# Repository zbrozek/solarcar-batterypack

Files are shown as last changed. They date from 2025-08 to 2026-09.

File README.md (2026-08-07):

# Open-source battery pack for solar cars
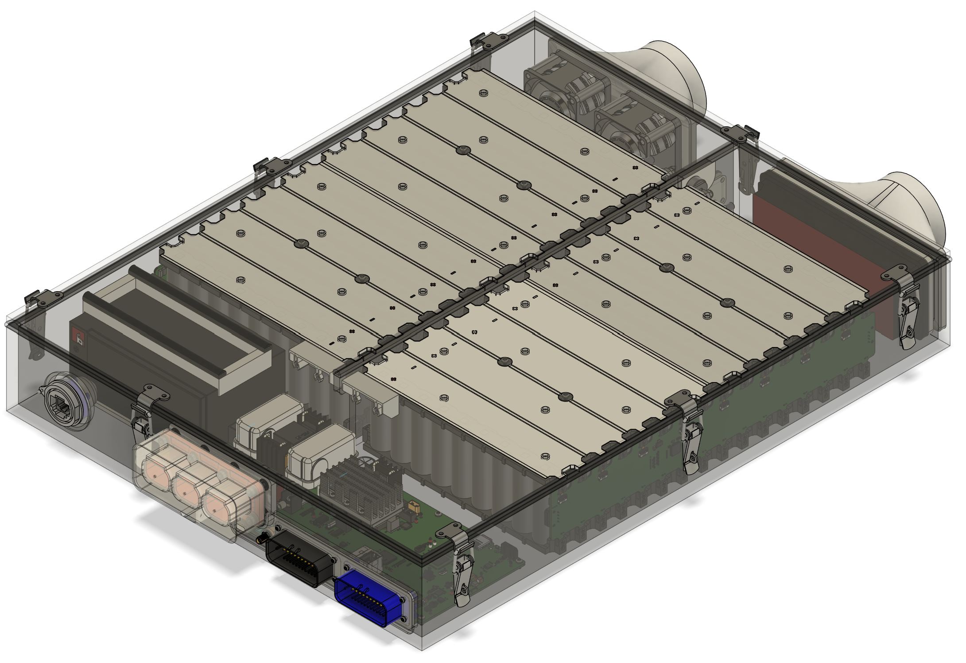
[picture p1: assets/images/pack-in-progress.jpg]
Image of battery pack


## What is this?
This is the mechanical and electronic design for a battery pack intended for solar cars competing in common races like ASC or WSC. It's designed to be reasonably easy to fabricate and assemble, but without significantly compromising the quality of the design.

## Who are you?
I'm Sasha Zbrozek and I was trained as an electrical engineer. I was on Stanford's solar car team from 2006 through 2010 and continue to participate with them and the broader solar car community from the comfort of my golden years. I have a normal day job that takes up most of my time, but we've all got to have hobbies.

## Why did you make this?
I participated as a staff member in the 2025 Formula Sun Grand Prix and enjoyed working with the students immensely. I think the community would benefit from having more open-source content available for students to take, modify, and improve.

And why a battery pack specifically? I felt that many cars under-engineered them and that there was a lot of room to try and introduce improvements that would have both performance and safety benefits for solar racing as a whole.

## Are you going to open-source the BMS too?
I did! Check the "bms" folder. This is an expansive design with way more features that most teams are going to use. There's a lot of electronic content in there that teams might want to use even if they aren't using this design in its totality. Check out:
- The MP6519 current regulator sheet for contactor coil economization.
- The HV architecture page and its very-aggressive precharge.
- The HV bleed page for an extremely simple DC bus safety enhancement implementation.

## Key design decisions and their motivations
### 32s9p arrangement
This pack is a 32 series, 9 parallel (32s9p) arrangement of [21700 cells](https://www.molicel.com/wp-content/uploads/Product-Data-Sheet-of-INR-21700-P50B-80122.pdf). This gives 134.4 volts top-of-charge with typical NMC cells. Using a power-of-two number of cells in series makes for really convenient bussing, allowing all bolted terminals to be on the top of the modules and for a wide range of module shapes. The voltage is reasonably safe for the Wavesculptor 22 and matches well with the super-beefy [MDE 30KPA132A TVS diode](https://mm.digikey.com/Volume0/opasdata/d220001/medias/docus/4180/30KPA_Series.pdf).

### Hybrid bus bars
Simple nickel sheet is pretty resistive and also dense. This design uses [aluminum bus bars with nickel inserts](https://www.everbestbattery.com/index.php?m=home&c=View&a=index&aid=171) for easy welding and high conductivity. Folded sheet metal also affords the opportunity for built-in studs for easy bolting where bolted joints cannot be avoided.

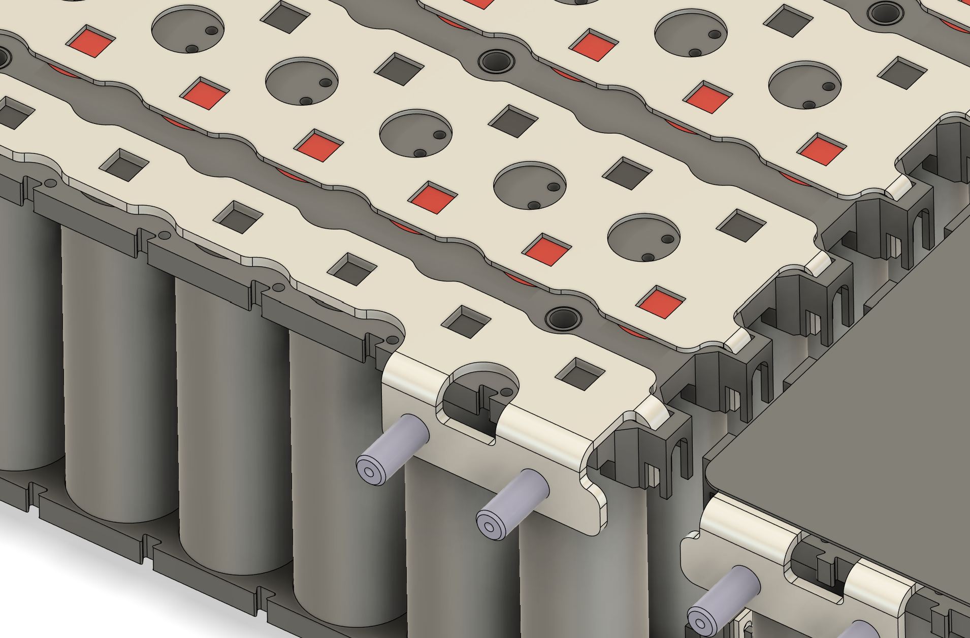
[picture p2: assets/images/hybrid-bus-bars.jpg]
Image of bus bars


### Large modules
This design uses only two 16s9p modules in order to dramatically cut down on the number of high-current bolted joints. Those are failure-prone and can easily cause battery pack fires by igniting nearby plastics if the bolted joints lose preload and become high impedance.

This is likely to be a controversial choice; teams often want their packs to be more modular in order to have a smaller minimum serviceable unit. In my experience, packs get built once and then basically never touched again outside of reworks to address manufacturing defects. My goal is to enable a high-quality module to be built, tested, and installed once.

### Cell monitoring on the side of the module
There is a large PCBA that mounts to the side of the module and is supposed to hold all of the cell monitoring and balancing electronics. This is to try and reduce the amount of wire harnessing inside of the battery pack, which is often failure-prone and easily shorted by accident.

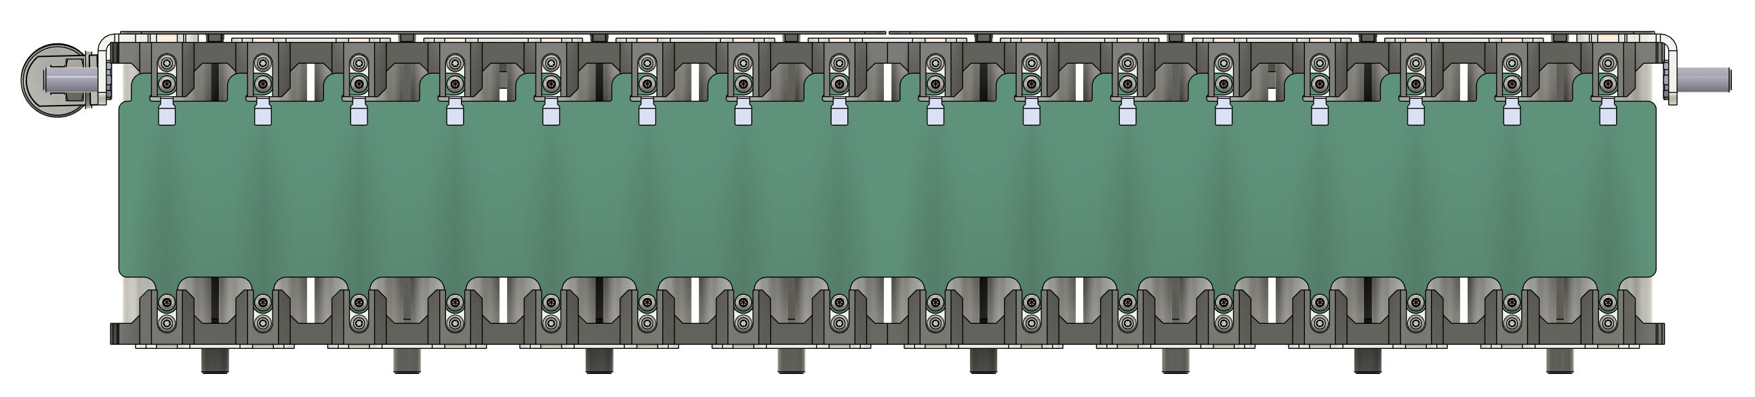
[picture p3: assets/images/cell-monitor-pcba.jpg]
Image of cell monitoring PCBA


### Mostly sealed
Aside from the deliberate air ingest and exhaust paths, the battery pack is theoretically sealed (assuming good manufacturing quality). Solar cars don't always enjoy sunny weather, so it's important to keep dust and water out. It uses the engine air filter to keep out dust.

### 3D-printed cell spacer plates
The cell spacer plates are intended to be 3D printed in [PC FR](https://us.store.bambulab.com/products/pc-fr) with a 0.2 mm nozzle. I used a Bambu H2D. There are a number of features that would be difficult or impossible to replicate without 3D printing, like the zero-draft shields that prevent you from losing screws into the forest of cells:

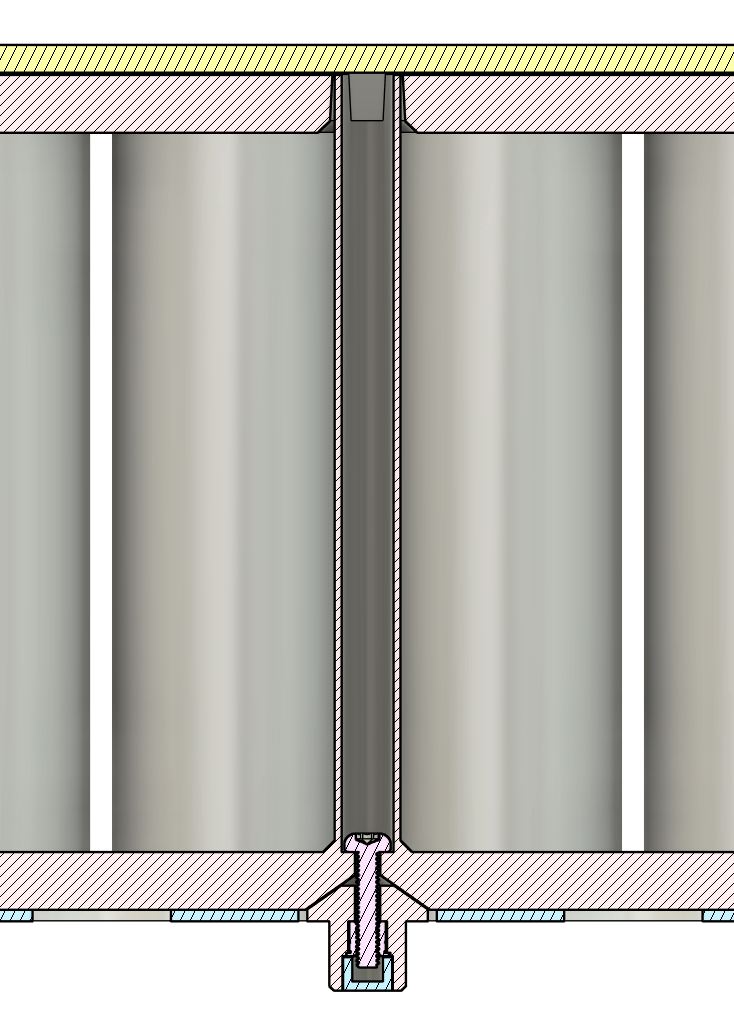
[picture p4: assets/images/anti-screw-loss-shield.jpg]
Image of an anti-screw-loss shield.


...or the fluid channels that deliver low-viscosity glue to hold the cells in place:

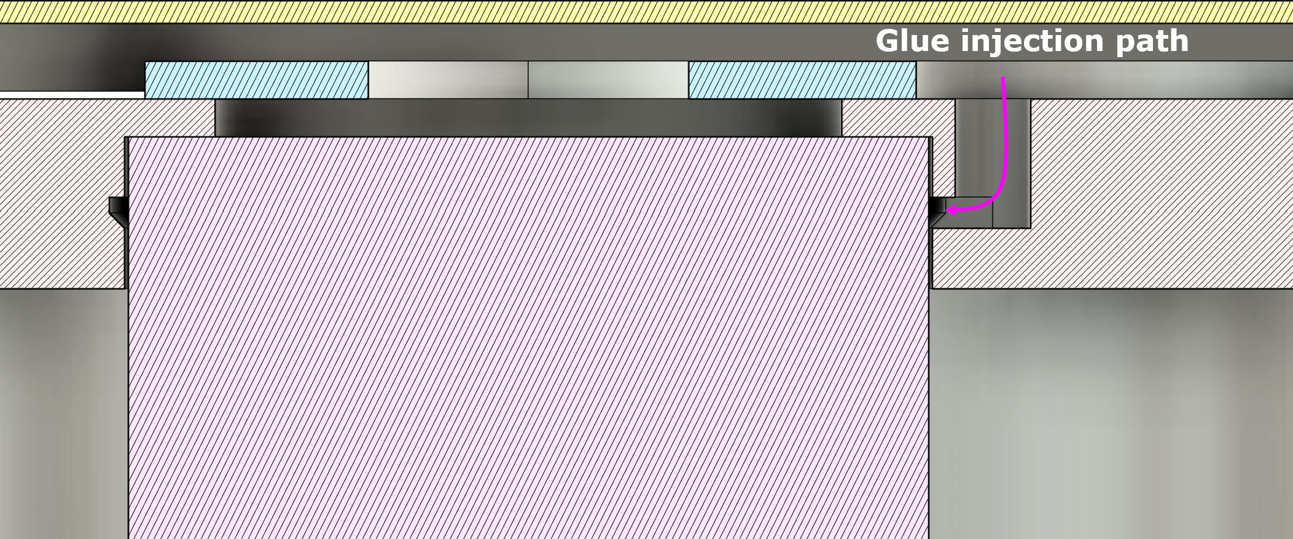
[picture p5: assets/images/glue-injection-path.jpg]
Image of a fluid channel for glue delivery for cell retention.


**Do not print parts without calibrated shrinkage calibration.** This design is not tolerant of undersized plastic parts.

### Mid-pack main fuse
A mid-pack fuse is a convenient way to halve the available electric potential (and thus quarter the available fault power) after a fault or during service. I prefer them to high- or low-side fuses. The mid-pack installation location also leverages the pack symmetry to reduce the total number of bolted joints.

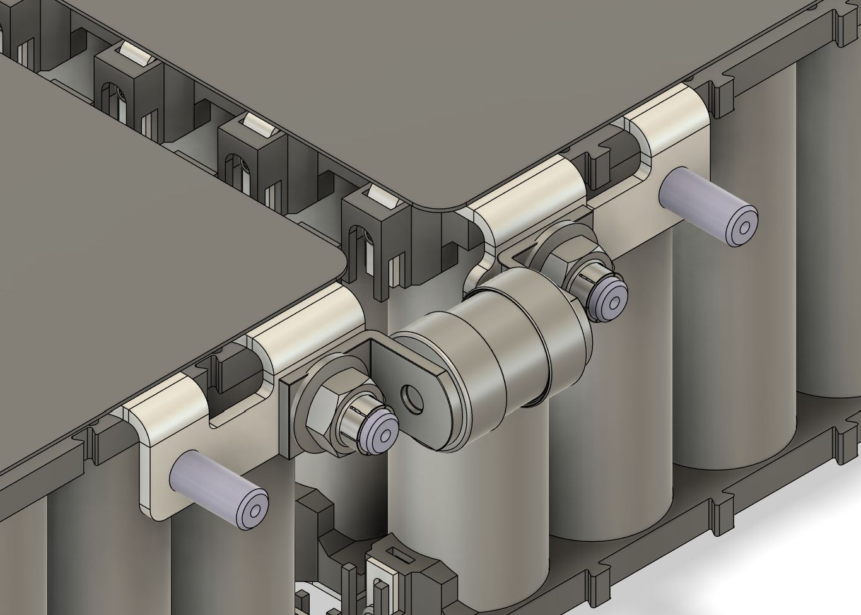
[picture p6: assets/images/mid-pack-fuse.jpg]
Image of a fuse installed at the pack midpoint.


### Shields
There are baffles that make it difficult to accidentally contact the sense taps on the bent parts of the bus bars:

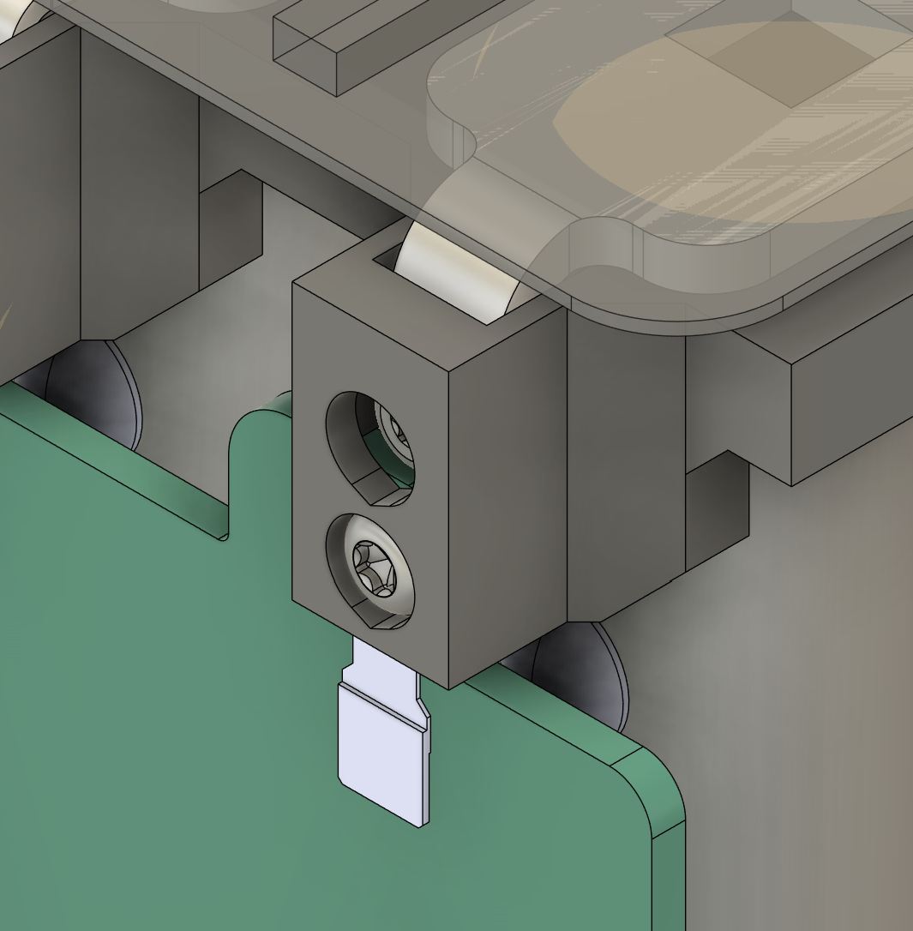
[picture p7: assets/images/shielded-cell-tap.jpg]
Image of a voltage sense tap with shielding plastic which makes it hard to accidentally contact the terminal.


There are also shields which go on the top side of the modules to reduce risks associated with leans and drops:

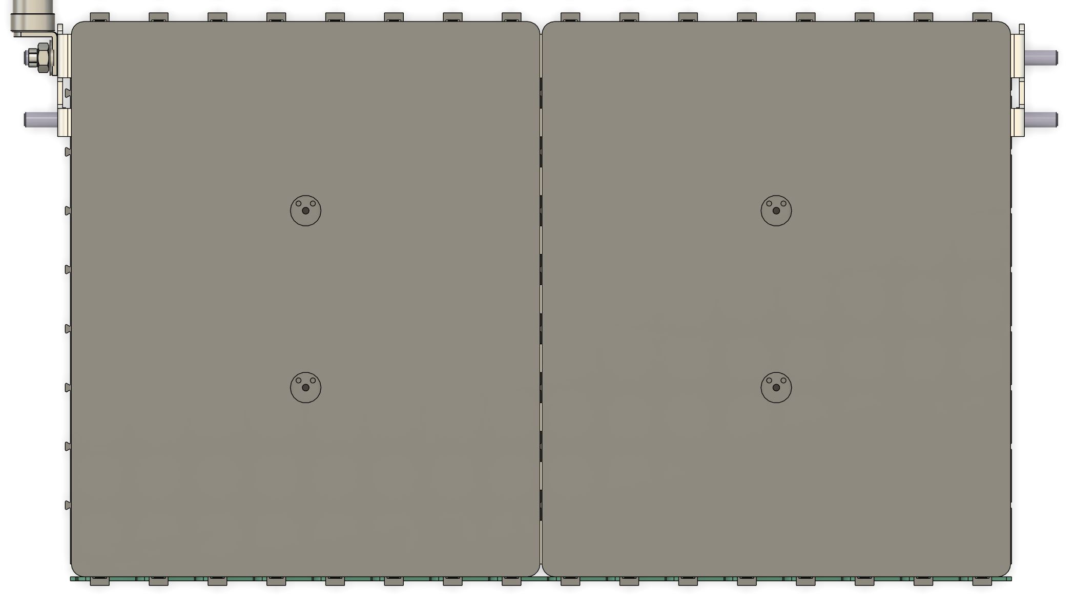
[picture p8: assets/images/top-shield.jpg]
Image of a plastic shields covering bus bars.


### Assembly aids
This design will come with a number of assembly aids to help with ergonomics, safety, or assembly quality. The first of these is a temporary handle that gets attached via screws from above while lifting and lowering the large modules into place into the battery pack.

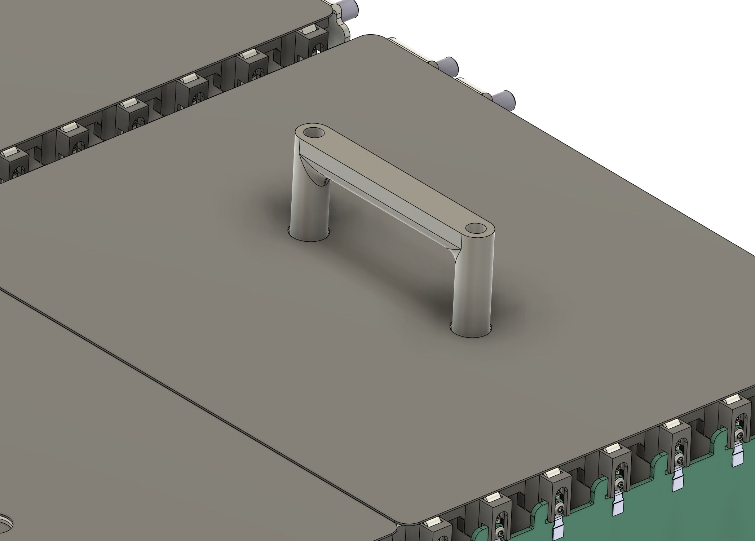
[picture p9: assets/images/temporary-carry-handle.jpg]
Image of a carry handle.


## What's not done yet?
Lots! Off the top of my head:
- There is no plug (airflow baffle) for the harness passthrough between the two cell monitoring boards.
- There is no fuse cover yet.
- I don't like the LV battery retention scheme and will probably do it again.
- Need to design assembly aids for centering the aluminum plates when gluing them to the chassis.
- Need to design assembly aids for setting the hasp Z height correctly.

## How do I use this?
A team looking to use this design will probably want to fork it and modify it to suit their vehicle. If you have any ideas for improvements, please file issues or create PRs and I'll consider including them upstream. Note that WSC and ASC have differing pack energy limitations, and so you may need to alter the number of parallel cells to match.

As this design matures I'll create additional documentation for things like the shopping list, tools needed for fabrication, and an assembly guide. For now, you'll need at least these tools and capabilities to reproduce the design:

- Ability to buy things from China with a wire transfer (bus bars)
- Ability to buy things from typical online vendors with a credit card (everything else)
- Ability to fixture an assembly and use epoxy to put it together
- Cell spot welding
- 3D printing in appropriate materials, primarily PC FR.
- Routing / milling of large sandwich panels
- Standard and long reach Torx drivers

## What are current versions?
I really need to use the GitHub release feature to make cohesive bundles of buildable artifacts. Until then, if you're building _right now_:
- The mechanical design is up-to-date. If there's a file missing, please file an issue.
- bms_afe-1_1
- Don't build any bms_afe_tester for now. That design is getting overhauled.
- bms_mainboard-1_0 (1.1 is coming end of August 2026)
- bms_fan_breakout-1_0

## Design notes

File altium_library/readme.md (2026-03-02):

# Theory of operation

These libraries are stored in CSV files, one table per file. Each table has fields that point to specific SchLib and PcbLib files and entries for symbols and footprints. The Windows ODBC system provides a local connection to the files.

Altium uses the dblib file to know what database to use. It also specifies field mappings for each table (CSV file). A user needs to use the "ODBC data sources (64-bit)" tool to get Windows to expose the CSV files as a SQL database.

# Getting started

Under the "User DSN" tab, hit "add", then select "Microsoft Access text driver". Give it the name "solarcar-altium-db", uncheck "use current directory", and select the "tables" directory in this repository. "OK" all the way out of the tool, restart Altium, and ensure that the dblib can connect to the ODBC provider and open the tables.

# Scripts

In the 'scripts' folder are some tools for downloading the JLCPCB library from yaqwsx. It'll come as a multi-part zip containing a sqlite database. The other tool parses that out into various CSV tables for use with Altium.

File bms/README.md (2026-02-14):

## bms_mainboard

Overall, this is a complicated and excessive kitchen sink of functionality. Its primary function is managing the battery pack state machine and driving the contactors accordingly. Beyond that, however, it is effectively a full central vehicle computer. There are some choices that seasoned solar car teams might find unusual.

The contactors are provided onboard. Most solar cars use dramatically bigger wires and contactors than they actually need. By right-sizing these devices, they can fit onto a PCBA. Current sensing is done via onboard shunt resistors in order to avoid more interconnects. This simplifies the wiring of the battery pack tremendously, reducing opportunities for errors and failures. There is also an automatic high voltage bus discharge when the system is powered down. All three contactors are driven with current regulators, enabling fine-grained control of coil currents in order to reduce system power consumption.

An onboard Ethernet switch provides Ethernet connectivity from the onboard STM32 microcontroller both to other on-vehicle devices as well as to an uncommitted RJ-45 receptacle intended for easy debugging. Some - maybe most - teams won't utilize this feature, preferring to stick to the more-familiar CAN (also provided). Beyond being simply much faster, Ethernet also offers point-to-point links which make the network (mostly) topology insensitive. There is no worrying about whether or not the bus remains terminated as the system topology changes.

The exception to the above is the speculative inclusion of a 10BASE-T1S PHY on the topshell-facing (blue Ampseal 35-position) connector. This is the IEEE 802.3 committee's answer to CAN. It is a 10 mbps multi-drop physical layer for Ethernet that carries traditional Ethernet frames. I will very-likely design MPPTs that use this bus. 

There are also some affordances for improved data gathering about the vehicle. An onboard IMU (3-axis acceleromter plus 3-axis gyroscope) can be used to capture information about vehicle dynamics or to try and estimate incline. An onboard GNSS receiver can be used to provide system time and capture vehicle location or to calibrate wheel odometry. An onboard MicroSD slot allows teams to log telemetry data locally in order to be independent of wireless telemetry systems.

An isolated DC/DC converter produces the low voltage power for the vehicle. It is permanently connected to a low voltage (nominally "12 volt") battery. That battery floats the low voltage bus, absorbing transient loads, but providing net-zero energy to the system. Hypercompetitive teams will probably be annoyed that the system does not afford a battery for allowed off-the-books loads. This is an opinionated choice on my part; I think reliability is more important and this reduces the amount of system state that needs to be tracked and babysat.

There is a current-loop called "EDISC" that must be completed in order for the BMS to receive power. This is intended to be sent to any number of series-connected on/off switches to turn the car on and off. A potentially-controversial feature is the ability for the main microcontroller tor read that loop and force-keepalive the system. This is intended to enable software-driven soft-shutdown procedures.

Finally, there are some protected high-side switches that can be used to drive lights or horns or other loads, as well as some analog and digital inputs for things like throttle sensors and switches.

## bms_afe

The mainboard does *not* sense battery voltages. The "analog front end" board does. It is mounted directly to the battery module to minimize pack wiring and opportunities for failure. This is admittedly annoying to assemble, but since that is a one-time procedure I consider it to be tolerable.

It is built around a TI BQ79616 cell monitoring chip and follows the provided application schematic closely. The board uses the eight remaining GPIO pins (which can be multiplexed to the on-chip ADC) to read NTC thermistors.

These boards can be connected to the mainboard or daisy-chained via twisted pair cables.

## bms_afe_tester

This is a development and test tool. It mates to the AFE board and has sixteen adjustable-output isolated flyback converters to drive the cell tap inputs. It's powered from USB-C PD at 12 volts and can communicate via a second USB-C port or via Ethernet. Hopefully teams use this for scripted automatic testing of their BMS software.

Another use for this is during scrutineering. I hope that teams will bring spare AFE boards and an AFE tester board so that they can easily demonstrate BMS behavior to scrutineers. Clip points are provided in case a team wants to override a flyback's output with an external supply. If doing that, set that channel's output to its lowest-possible voltage and then externally drive to a higher voltage.

## bms_fan_breakout

This is a simple board to break out from an 8-pin FPC cable to two PC-compatible 4-pin fan headers.

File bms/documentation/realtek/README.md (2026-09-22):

The RTL8152B does not have vendor-available documentation, yet it is easily purchaseable through LCSC. I've copied references and tools found on the internet into this repo for ease of use.

[RTL8152B-VB-CG datasheet](https://ftp.infania.net/pub/Windows%20Drivers/Realtek/NIC/RTL8152B-VB-CG_Datasheet_1.2.zip)
[RTL8152B-VB-CG reference schematic](https://ftp.infania.net/pub/Windows%20Drivers/Realtek/NIC/RTL8152B_REFERENCE_SCHEMATIC_V103.zip)
[Windows PG Tool](https://download3.terra-master.com/Utilities/A%20USBLAN%202.5G/A-USBLAN-2.5G_WIN_USB_PGTOOL_v2.0.13_V3.zip)
[Linux PG Tool](https://chromium.googlesource.com/chromiumos/third_party/hdctools/+/master/servo/scripts/servo_mfg/rtunicpg-x86_64)

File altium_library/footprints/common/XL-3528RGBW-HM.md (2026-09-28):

# XINGLIGHT XL-3528RGBW-HM 3D model

`XL-3528RGBW-HM.step` is a colored STEP AP214 file in millimeters. Five solids
represent the molded body and four contacts. The flat black bezel and opaque
white diffuser are colored faces of the body, so they add no thickness or
extra solids. This is the unlit appearance. Hidden dies, bond wires and
internal leadframe geometry are omitted.

## Altium placement

The model matches the origin and pin orientation of `LED_RGB_SMD3528-4P` in
`led_rgb_smd3528-4p.PcbLib`. Use X=0, Y=0, Z=0, rotations=0, scale=1.
The contact undersides are at **Z=0**, with the top at **Z=1.90 mm**.
Looking down from +Z with +Y upward, the marked pin-1 corner is lower right.

| Pin | Function | Existing pad center X | Existing pad center Y |
| --- | --- | ---: | ---: |
| 1 | Red cathode | +1.35 | -0.75 |
| 2 | Common anode | -1.35 | -0.75 |
| 3 | Green cathode | +1.35 | +0.75 |
| 4 | Blue cathode | -1.35 | +0.75 |

Pads are 0.90 x 0.90 mm. The four contacts fit entirely inside their matching
pad outlines. Their envelope centers are X=+/-1.39 mm and Y=+/-0.75 mm.

## Dimensions and sources

The repository's [XINGLIGHT datasheet](../../../../bms/documentation/xinglight/XL-3528RGBW-HM.pdf),
page 9, supplies the dimensions and pinout. Page 1 supplies the exterior
reference illustration. Public manufacturer references are the
[product page](https://www.xinglight.cn/index.php?c=show&id=3412) and its
[datasheet](https://www.xinglight.cn/uploadfile/202511/505682b0e27017b.pdf).

| Feature | Model dimension (mm) |
| --- | ---: |
| Overall X, including contacts | 3.50 |
| Body maximum X | 3.20 |
| Body Y | 2.80 |
| Overall height | 1.90 |
| Contact width along Y | 0.70 |
| Contact pitch along Y | 1.50 |
| Contact rise above seating plane | 1.10 |
| Underside contact envelope length along X | 0.72 |

The drawing also labels the underside contact gap as 2.0 mm. That differs
from 3.50 - 2 x 0.72 = 2.06 mm. The model preserves the stated overall width
and contact length, giving a 2.06 mm gap. The 0.06 mm difference is within
the drawing's general +/-0.25 mm tolerance. Nominal dimensions are modeled;
this is not a maximum-tolerance clearance envelope.

The following undimensioned details are approximate: 2.40 mm diffuser
diameter, 0.20 mm contact-foot thickness and housing standoff, 0.05 mm side
draft in X, 0.04 mm contact bend radius, and the roughly 0.6 mm polarity
corner ending 0.3 mm below the top. The circular diffuser is flush and opaque,
consistent with the mist-white material and reference illustration. Colors
are approximate. Fine underside molding relief is simplified.

The old footprint extrusion is a 3.2 x 3.2 mm square. This model follows the
datasheet's 3.2 x 2.8 mm molded body. The PcbLib has not been modified.

## Validation and regeneration

The exported file was re-imported into FreeCAD/Open CASCADE and checked for
five valid solids, preserved face colors, contact surfaces at Z=0, contact
alignment within the existing pads, and the 3.50 x 2.80 x 1.90 mm overall
envelope. No solids overlap in volume. Isometric, top and bottom renders of
the re-imported STEP were inspected. Import into Altium itself was not tested.

The generator is `../../scripts/build_xl3528_step.py`. From the repository root:

```powershell
& 'C:\Program Files\FreeCAD 1.0\bin\python.exe' altium_library\scripts\build_xl3528_step.py --render --qa-dir tmp\xl3528
```

FreeCAD 1.0 was used. VTK is required only for the optional preview render.
The generator needs no network access or additional asset files.

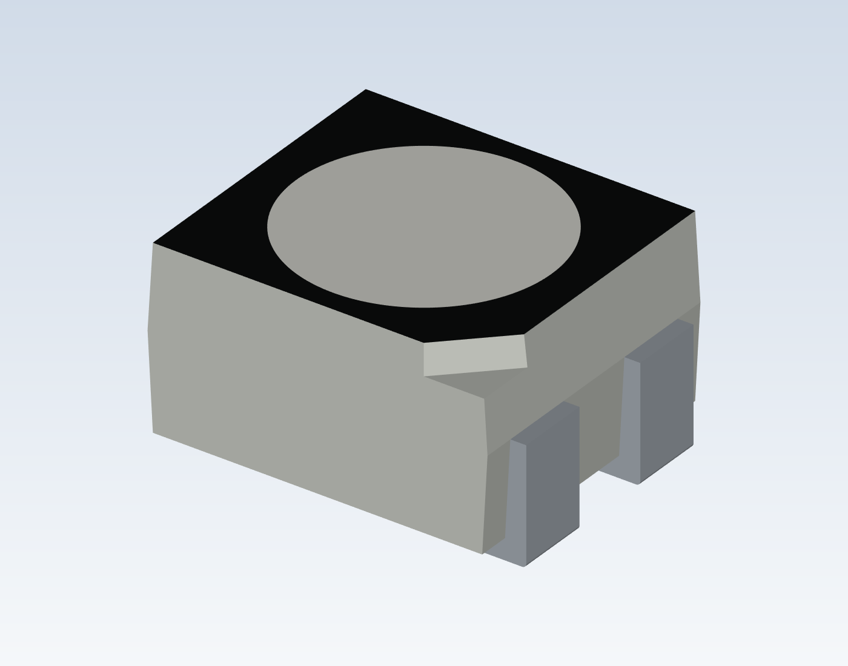
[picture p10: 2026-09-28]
altium_library/footprints/common/XL-3528RGBW-HM.png

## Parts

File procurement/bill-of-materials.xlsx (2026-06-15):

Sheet: BOM
Quantity | Item | Where used | Supplier | Supplier part | Notes
2 | End collector (mirrored) | End terminal collector plate of cell stack | Everbest Battery (http://www.everbestbattery.com/) | N/A | Order several spares, send .STEP to lily@everbestbattery.com
2 | End collector | End terminal collector plate of cell stack | Everbest Battery (http://www.everbestbattery.com/) | N/A | Order several spares, send .STEP to lily@everbestbattery.com
30 | Basic collector | Standard collector plate within cell stack | Everbest Battery (http://www.everbestbattery.com/) | N/A | Order plenty of spares, send .STEP to lily@everbestbattery.com
8 | Small latches | Box lid retention | Amazon | B0CGVPR5RZ (https://www.amazon.com/dp/B0CGVPR5RZ) | One box provides 8 pieces; throw away strikes.
8 | Small strike plate for latches | Box lid retention | Amazon | B0DL9TXC2P (https://www.amazon.com/dp/B0DL9TXC2P) | One box provides 10 pieces.
1 | EPDM self-adhesive weather strip | Box lid seal | Home Depot | 625515 (https://www.homedepot.com/p/Frost-King-5-16-in-x-1-4-in-x-17-ft-Black-EPDM-Cellular-Rubber-Weatherstrip-Tape-V25BK/202844545) | One box provides 17 feet.
6 | 8x3 cylindrical magnet | Fan box collar | Amazon | B0CDGYTLH6 (https://www.amazon.com/dp/B0CDGYTLH6) | One box provides 200 pieces.
6 | 8x3 cylindrical magnet | Fan duct collar | Amazon | B0CDGYTLH6 (https://www.amazon.com/dp/B0CDGYTLH6) | One box provides 200 pieces.
8 | 8x3 cylindrical magnet | Filter box collar | Amazon | B0CDGYTLH6 (https://www.amazon.com/dp/B0CDGYTLH6) | One box provides 200 pieces.
8 | 8x3 cylindrical magnet | Filter duct collar | Amazon | B0CDGYTLH6 (https://www.amazon.com/dp/B0CDGYTLH6) | One box provides 200 pieces.
8 | M5x14 thread-forming | Fan mounting | McMaster | 95893A247 (https://www.mcmaster.com/95893A247) | One box provides 25 pieces.
~~2~~ | ~~Sanyo Denki 9HV06~~ | ~~Fan~~ | ~~Digikey~~ | ~~1688-2189-ND~~ (https://www.digikey.com/en/products/detail/sanyo-denki-america-inc/9HV0612P1J001/8285336) | ~~This is almost certainly severe overkill.~~
2 | Noctua 60mm 4-wire fan | Fan | Amazon | B00VXTANZ4 (https://www.amazon.com/Noctua-NF-A6x25-PWM-Premium-Quiet/dp/B00VXTANZ4) | This is more reasonable.
1 | Renault Clio engine air filter | Filter housing | KN Filters | 33-2860 (https://www.knfilters.com/33-2860-replacement-air-filter)
1 | Loctite E-60HP epoxy | General purpose toughened epoxy | McMaster | 1765A52 (https://www.mcmaster.com/1765A52)
2 | Low viscosity cyanoacrylate glue | Spacer plate adhesive | Amazon | B0DT14TGDY (https://www.amazon.com/dp/B0DT14TGDY) | One bottle is enough for a little bit more than one module.
1 | High viscosity cyanoacrylate glue | General purpose cyanoacrylate | Amazon | B0006HUJCQ (https://www.amazon.com/Loctite-1364076-Super-Squeeze-Liquid/dp/B0006HUJCQ) | Can build more than one battery pack per tube.
4 | M6 flex-top lock nuts | Fuse and main terminal bolted joints | McMaster | 94560A060 (https://www.mcmaster.com/94560A060)
4 | M6 conical washer | Fuse and main terminal bolted joints | McMaster | 91477A161 (https://www.mcmaster.com/91477A161) | One box provides 25 pieces.
1 | NO-OX-ID A-Special contact grease | Electrical bolted joints | Amazon | B00HDF9EXE (https://www.amazon.com/dp/B00HDF9EXE) | Can build more than one battery pack per tub.
64 | M2 thin square nuts | Inserted into cell spacer plate for PCBA retention | McMaster | 97258A121 (https://www.mcmaster.com/97258A121) | One box provides 25 pieces.
64 | M2x6 Torx | Retains PCBA to cell spacer plate | McMaster | 90362A137 (https://www.mcmaster.com/90362A137) | One box provides 100 pieces.
64 | M2 conical washer | Between AFE PCBA and screw head | McMaster | 91477A122 (https://www.mcmaster.com/91477A122/) | One box provides 50 pieces.
32 | M2 press-fit standoffs | Mushroom inserts | McMaster | 92985A818 (https://www.mcmaster.com/92985A818) | One box provides 25 pieces.
32 | M2x10 Torx | Retains modules into mushroom inserts | McMaster | 90362A139 (https://www.mcmaster.com/90362A139) | One box provides 100 pieces.
128 | M2x5 Plastite Torx | Bus bar to spacer retention | McMaster | 99397A066 (https://www.mcmaster.com/99397A066) | One box provides 50 pieces.
8 | M4x18 socket head | HVA280 retention | McMaster | 91292A043 (https://www.mcmaster.com/91292A043/) | One box provides 100 pieces.
8 | M4 flat washer | HVA280 retention | McMaster | 93475A230 (https://www.mcmaster.com/93475A230/) | One box provides 100 pieces.
8 | M3x14 Plastite Torx | Temporary handle retention | McMaster | 99397A450 (https://www.mcmaster.com/99397A450) | One box provides 50 pieces.
6 | M3x25 Torx | Vicor retention | McMaster | 90362A156 (https://www.mcmaster.com/90362A156/) | One box provides 100 pieces.
4 | M3x6 Torx | Fan adapter PCB retention | McMaster | 90362A113 (https://www.mcmaster.com/90362A113/) | One box provides 100 pieces.
4 | M3x3.4 brass heat-set insert | Fan adapter PCB retention | McMaster | 94459A769 (https://www.mcmaster.com/94459A769/) | One box provides 50 pieces.
2 | M6 6 AWG ring terminal | Bus bar to wire connection | Digikey | 277-11163-ND (https://www.digikey.com/en/products/detail/phoenix-contact/3240090/3603837) | Phoenix Contact 3240090.
4 | M3 flex-top lock nuts | BMS contactor coil connection | McMaster | 94560A111 (https://www.mcmaster.com/94560A111/) | Sold each
4 | M3 conical washer | BMS contactor coil connection, between nut and PCBA | Mcmaster | 91477A121 (https://www.mcmaster.com/91477A121/) | One box provides 100 pieces.
4 | M4 flex-top lock nuts | BMS contactor current carrying connection | McMaster | 94560A112 (https://www.mcmaster.com/94560A112/) | Sold each
4 | M4 conical washer | BMS contactor current carrying connection, between nut and PCBA | McMaster | 91477A141 (https://www.mcmaster.com/91477A141/) | One box provides 25 pieces.
2 | M4 6-8 AWG ring terminal | BMS mainboard to bus bar wire connection | Digikey | WM7288-ND (https://www.digikey.com/en/products/detail/molex/0191930200/3044482) | Molex 0191930200.
6 | M4 10-14 AWG ring terminal | BMS mainboard to enclosure wire connection | Digikey | 277-11157-ND (https://www.digikey.com/en/products/detail/phoenix-contact/3240083/3603843) | Phoenix Contact 3240083.
8 | M4 conical washer | BMS mainboard to wire connection | McMaster | 91477A141 (https://www.mcmaster.com/91477A141/) | One box provides 25 pieces.
8 | M4x8 Torx | BMS mainboard wire fasteners | McMaster | 90362A118 (https://www.mcmaster.com/90362A118/) | One box provides 100 pieces.
1 | Red & black 6 AWG silicone wire | BMS mainboard to bus bar wires | Amazon | B0BTLFNLLY (https://www.amazon.com/Dastard-Flexible-Insulated-Separated%E3%80%91High-Temperature/dp/B0BTLFNLLY) | Highly flexible to make internal box routing easier.
1 | Red & black 8 AWG silicone wire | BMS mainboard to HVA280 wires, if they fit. | Amazon | B09ZTFHNLD (https://www.amazon.com/ZIGPEO-Silicone-Flexible-Stranded-Copper/dp/B09ZTFHNLD/) | Highly flexible to make internal box routing easier.
1 | Red & black 10 AWG silicone wire | BMS mainboard to HVA280 wires | Amazon | B07Z4S98J4 (https://www.amazon.com/Silicone-Electrical-Flexible-Strands-Battery/dp/B07Z4S98J4/) | Highly flexible to make internal box routing easier.
9 | M3x6 Torx | BMS mainboard PCB retention | McMaster | 90362A113 (https://www.mcmaster.com/90362A113/) | One box provides 100 pieces.
9 | M3x3.4 brass heat-set insert | BMS mainboard PCB retention | McMaster | 94459A769 (https://www.mcmaster.com/94459A769/) | One box provides 50 pieces.
8 | M2.63x8 thread-forming Torx | BMS Ampseal to front panel fastener | McMaster | 99397A351 (https://www.mcmaster.com/99397A351/) | One box provides 50 pieces.
2 | M2x5 Plastite Torx | BMS security tape frame retention | McMaster | 99397A066 (https://www.mcmaster.com/99397A066) | One box provides 50 pieces.
1 | IP68 Ethernet passthrough | Box connector face | Digikey | SAM9120-ND (https://www.digikey.com/en/products/detail/samtec-inc/SCRES-G-00-50-D-C5E/6613670)
1 | Ethernet dust cover | Box connector face | Digikey | SAM8760-ND (https://www.digikey.com/en/products/detail/samtec-inc/DCA-17-01/2176473)
16 | 10k NTC thermistor | Side of module nearest monitoring PCBA | Digikey | BC2792-ND (https://www.digikey.com/en/products/detail/vishay-beyschlag-draloric-bc-components/NTCAFLEX05103HH/3712579)
1 | 100 amp fuse | Mid-pack fuse between modules | Digikey | 5923-0AFGBK100SBA-ND (https://www.digikey.com/en/products/detail/bel-fuse-inc/0AFGBK100SBA/16686101) | You can pick other values to suit your needs
1 | 9 mm diameter adhesive heat shrink | Wire to ring terminal conections | Digikey | SCT-NO.2-E5-0-STK-ND (https://www.digikey.com/en/products/detail/te-connectivity-raychem-cable-protection/SCT-NO-2-E5-0-STK/3466356)

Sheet: Race service hardware
Quantity | Item | Where used | Supplier | Supplier part | Notes
1 | 100 amp fuse | Mid-pack fuse between modules | Digikey | 5923-0AFGBK100SBA-ND (https://www.digikey.com/en/products/detail/bel-fuse-inc/0AFGBK100SBA/16686101) | You can pick other values to suit your needs
1 | EPDM self-adhesive weather strip | Box lid seal | Home Depot | 625515 (https://www.homedepot.com/p/Frost-King-5-16-in-x-1-4-in-x-17-ft-Black-EPDM-Cellular-Rubber-Weatherstrip-Tape-V25BK/202844545) | One box provides 17 feet.
4 | M6 flex-top lock nuts | Fuse and main terminal bolted joints | McMaster | 94560A060 (https://www.mcmaster.com/94560A060)
4 | M6 conical washer | Fuse and main terminal bolted joints | McMaster | 91477A161 (https://www.mcmaster.com/91477A161) | One box provides 25 pieces.
1 | NO-OX-ID A-Special contact grease | Electrical bolted joints | Amazon | B00HDF9EXE (https://www.amazon.com/dp/B00HDF9EXE) | Can build more than one battery pack per tub.
64 | M2x6 Torx | Retains PCBA to cell spacer plate | McMaster | 90362A137 (https://www.mcmaster.com/90362A137) | One box provides 100 pieces.
64 | M2 conical washer | Between AFE PCBA and screw head | McMaster | 91477A122 (https://www.mcmaster.com/91477A122/) | One box provides 50 pieces.
32 | M2x10 Torx | Retains modules into mushroom inserts | McMaster | 90362A139 (https://www.mcmaster.com/90362A139) | One box provides 100 pieces.
2 | M6 6 AWG ring terminal | Bus bar to wire connection | Digikey | 277-11163-ND (https://www.digikey.com/en/products/detail/phoenix-contact/3240090/3603837) | Phoenix Contact 3240090.
2 | M4 6-8 AWG ring terminal | BMS mainboard to bus bar wire connection | Digikey | WM7288-ND (https://www.digikey.com/en/products/detail/molex/0191930200/3044482) | Molex 0191930200.
6 | M4 10-14 AWG ring terminal | BMS mainboard to enclosure wire connection | Digikey | 277-11157-ND (https://www.digikey.com/en/products/detail/phoenix-contact/3240083/3603843) | Phoenix Contact 3240083.
8 | M4 conical washer | BMS mainboard to wire connection | McMaster | 91477A141 (https://www.mcmaster.com/91477A141/) | One box provides 25 pieces.
8 | M4x8 Torx | BMS mainboard wire fasteners | McMaster | 90362A118 (https://www.mcmaster.com/90362A118/) | One box provides 100 pieces.
1 | Red & black 6 AWG silicone wire | BMS mainboard to bus bar wires | Amazon | B0BTLFNLLY (https://www.amazon.com/Dastard-Flexible-Insulated-Separated%E3%80%91High-Temperature/dp/B0BTLFNLLY) | Highly flexible to make internal box routing easier.
1 | Red & black 8 AWG silicone wire | BMS mainboard to HVA280 wires, if they fit. | Amazon | B09ZTFHNLD (https://www.amazon.com/ZIGPEO-Silicone-Flexible-Stranded-Copper/dp/B09ZTFHNLD/) | Highly flexible to make internal box routing easier.
1 | Red & black 10 AWG silicone wire | BMS mainboard to HVA280 wires | Amazon | B07Z4S98J4 (https://www.amazon.com/Silicone-Electrical-Flexible-Strands-Battery/dp/B07Z4S98J4/) | Highly flexible to make internal box routing easier.
9 | M3x6 Torx | BMS mainboard PCB retention | McMaster | 90362A113 (https://www.mcmaster.com/90362A113/) | One box provides 100 pieces.
8 | M2.63x8 thread-forming Torx | BMS Ampseal to front panel fastener | McMaster | 99397A351 (https://www.mcmaster.com/99397A351/) | One box provides 50 pieces.
1 | 9 mm diameter adhesive heat shrink | Wire to ring terminal conections | Digikey | SCT-NO.2-E5-0-STK-ND (https://www.digikey.com/en/products/detail/te-connectivity-raychem-cable-protection/SCT-NO-2-E5-0-STK/3466356)
4 | M3 flex-top lock nuts | BMS contactor coil connection | McMaster | 94560A111 (https://www.mcmaster.com/94560A111/) | Sold each
4 | M3 conical washer | BMS contactor coil connection, between nut and PCBA | Mcmaster | 91477A121 (https://www.mcmaster.com/91477A121/) | One box provides 100 pieces.
4 | M4 flex-top lock nuts | BMS contactor current carrying connection | McMaster | 94560A112 (https://www.mcmaster.com/94560A112/) | Sold each
4 | M4 conical washer | BMS contactor current carrying connection, between nut and PCBA | McMaster | 91477A141 (https://www.mcmaster.com/91477A141/) | One box provides 25 pieces.

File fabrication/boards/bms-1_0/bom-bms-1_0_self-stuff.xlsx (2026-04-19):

Quantity | Designator | Description | Manufacturer | Manufacturer Part Number | Supplier 1 | Supplier Part Number 1 | Supplier 2 | Supplier Part Number 2 | Footprint
2 | F1, F4 | FUSE EV 80A 200VDC 2P TERM | Eaton | ELV10-80-2P | Digikey | 283-ELV10-80-2P-ND |  |  | EATON_ELV10-xx-2P
1 | F2 | 15A 200 VDC Fuse Cartridge Through Hole | Eaton | ELV10-15-2P | Digikey | 283-ELV10-15-2P-ND |  |  | EATON_ELV10-xx-2P
1 | J8 | Conn RJ-45 F 8 POS 1.02mm Solder ST Thru-Hole 20 Terminal 1 Port Tray | Bel | V8BR-1AX1-GH | Digikey | 5923-V8BR-1AX1-GH-ND | LCSC | C5346729 | BELFUSE_V8BR-1AX1-GH
1 | H2 | Heat Sink, Aluminum | Vicor | 16495 | Digikey | 1102-1560-ND | Mouser | 492-16495
1 | H3 | Heat Sink, Aluminum | Vicor | 30183 | Digikey | 1102-1595-ND | Mouser | 492-30183 | VICOR_HEATSINK_30183
3 | HS1, HS2, HS3 | Heat Sink, 11ohm, Extruded, Clip, Longitudinal, Aluminum Alloy, Anodized | Ohmite | WA-T247-101E | Digikey | WA-T247-101E-ND |  |  | OHMITE_WA-T247-101E
8 | J3, J4, J5, J6, J18, J19, J20, J21 | POWER ELEMENT BUSH M4 12PIN | Wurth Electronics | 7461086 | Digikey | 732-3207-ND |  |  | WURTH_TERM_7461086
1 | J9 | CONN FFC VERT 8POS 1MM SMD | Wurth Elektronik | 686108183822 | Digikey | 732-6018-1-ND | Mouser | 710-686108183822 | WURTH_WR-FPC_1.00mm_686108183822
2 | K1, K3 | RELAY GEN PURPOSE SPST 60A 12V | Sensata | P126BDA | Digikey | 3596-P126BDA-ND | Mouser | 682-P126BDA | RELAY_P126
1 | K2 | General Purpose Relay 450VDC/10A | Fujitsu | FTR-J2AK006W | Verical | FTR-J2AK006W | Mouser | 817-FTR-J2AK006W | RELAY_FTR-J2
1 | U5 | APSM DCDC, 1 Output, 100W, Hybrid | Vicor | V110C12C100BG | Digikey | V110C12C100BG-ND
1 | U15 | 5V to 5V isolated power supply module | Recom | ROL-0505S | Digikey | 945-1949-5-ND |  |  | 4SIP
1 | J14 | SMA Connector Jack, Female Socket Panel Mount, Through Hole, Right Angle Solder, IP68 unmated | GCT (Gradconn) | RFPC-SMA14-FN-A | Digikey | 2072-RFPC-SMA14-FN-A-ND | LCSC | C3173272 | GCT_RFPC-SMA14-FN-A
1 | J12 | Conn Power PL 35 POS 4mm Solder RA Thru-Hole 35 Terminal 1 Port, BLACK | TE Connectivity | 1-776163-1 | Digikey | A106383-ND | LCSC | C596198 | TE_AMPSEAL_1-776163-1
1 | J13 | Conn Power PL 35 POS 4mm Solder RA Thru-Hole 35 Terminal 1 Port, BLUE | TE Connectivity | 1-776163-5 | Digikey | 1-776163-5-ND | LCSC | C17378321 | TE_AMPSEAL_1-776163-5
6 | H4, H5, H6, H14, H15, H16 | Standoff Round Swage F/F M3 X 0.5-THD Carbon Steel Electro-Tin ASTM B545 | PennEngineering | SMTSO-M3-2ET | Mouser | 153-SMTSO-M3-2ET | LCSC | C18212183 | SMTSO-M3-2ET
1 | C60 | Aluminum Electrolytic Capacitor, Polarized, Aluminum (wet), 220V, 20% +Tol, 20% -Tol, 220uF, Through Hole Mount | United Chemi-Con | EKXJ221ELL221MM25S | Digikey | 565-EKXJ221ELL221MM25S-ND | LCSC | C1600234 | CAP_1600X2700X750
2 | F3, F5 | Polymeric PTC Resettable Fuse 240V 2 A Ih Through Hole Radial, Disc | Bel Fuse Inc. | 0ZRE0200FF1A | Digikey | 5923-0ZRE0200FF1A-ND | LCSC |  | BELFUSE_0ZRE0200FF
7 | H7, H8, H9, H10, H11, H12, H13 | Pin Receptacle Connector 0.078" ~ 0.096" (1.98mm ~ 2.44mm) No Tail Solder | Preci-Dip | 15115-91-0710 | Digikey | 1212-15115-91-0710-ND |  |  | PRECI-DIP_15115-91-0710
2 | R82, R84 | RES TK FM 7.5 OHM 100W 1% TO247 | Ohmite | TEH100M7R50FE | Digikey | TEH100M7R50FE-ND | LCSC | C2641795 | TO-247-2_VERTICAL
1 | R112 | RES TK FM 470 OHM 100W 1% TO247 | Ohmite | TEH100M470RJE | Digikey | TEH100M470RJE-ND | LCSC | C2642463 | TO-247-2_VERTICAL
1 | U14 | 6-ch 2.5kV Isolator, 150M, 4/2, NB SOIC16, lead free | Skyworks Solutions | SI8662BB-B-IS1 | Digikey | SI8662BB-B-IS1-ND | LCSC | C430287 | 16SOIC150
1 | XF6 | Fuse Holder 30 A 500V 1 Circuit Blade Through Hole | Keystone Electronics | 3568 | Digikey | 36-3568-ND | LCSC | C3206956 | FUSEHOLDER_KEYSTONE_3568
3 | R80, R83, R89 | RES SMD 0.0005 OHM 1% 3W 2726 | Vishay Dale | WSL2726L5000FEB | Digikey | WSLQ-.0005CT-ND | LCSC | C4132421 | VISHAY_WSL2726
2 | R90, R160 | RES SMD 0.005 OHM 1% 3W 2726 | Vishay Dale | WSL27265L000FEB | Digikey | WSLQ-.005CT-ND | LCSC | C1517421 | VISHAY_WSL2726
1 | D9 | DIODE ZENER 56V 200MW SOD | onsemi | MM3Z56VC | Digikey | 488-MM3Z56VCCT-ND | LCSC | C891632 | SOD323
1 | X2 | CRYSTAL 32.768 KHZ 12.5 PF SMD | TXC CORPORATION | 9HT10-32.768KEZF-T | Digikey | 887-1507-1-ND | LCSC | C5932452 | XTAL_TXC_9HT10

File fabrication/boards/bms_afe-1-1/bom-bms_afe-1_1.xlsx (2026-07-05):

Comment | Designator | Footprint | JLCPCB Part #
CL10B474KA8NNNC | C1, C2, C3, C4, C5, C6, C7, C8, C9, C10, C11, C12, C13, C14, C15, C16, C17, C19, C20, C21, C22, C23, C24, C25, C26, C27, C28, C29, C30, C33, C35, C37, C38, C42, C44 | C0603 | C1623
CL10B105KA8NNNC | C18, C36, C39, C40 | C0603 | C29936
TCC1206X7R224K101FT | C31 | C1206 | C374077
CC0402KRX7R0BB103 | C32 | C0402 | C527014
CL05B104KB54PNC | C34, C41, C45A, C45B | C0402 | C307331
CL21B475KOFNNNE | C43 | C0805 | C107365
0402YA101JAT2A | C48A, C48B, C49A, C49B | C0402 | C2174471
LTST-C190KRKT | D1, D2, D3, D4, D5, D6, D7, D8, D9, D10, D11, D12, D13, D14, D15, D16 | LED_0603P_RED | C94869
PESD2USB3UX | D17A, D17B | 3SOT23 | C3708426
JFC2410-0500TS | F1, F2, F3, F4, F5, F6, F7, F8, F9, F10, F11, F12, F13, F14, F15, F16, F17, F18, F19 | JDTFUSE_JFC2410 | C136377
2005280040 | J1, J2, J3, J4, J5, J6, J7, J8 | MOLEX_FD19_1.00mm_2005280040 | C563728
43650-0204 | J9A, J9B | MOLEX_MICROFIT_0436500204 | C587652
NSV1C201MZ4T1G | Q1 | 4SOT223 | C86644
RC0402FR-07100RL | R1, R5, R9, R13, R17, R21, R25, R29, R33, R45, R49, R53, R57, R61, R63, R64, R65, R69, R73, R77 | R0402 | C106232
0402WGF1001TCE | R2, R6, R10, R14, R18, R22, R26, R30, R34, R46, R50, R54, R58, R62, R70, R74 | R0402 | C11702
RC2512FK-0730RL | R3, R4, R7, R8, R11, R12, R15, R16, R19, R20, R23, R24, R27, R28, R31, R32, R39, R44, R47, R48, R51, R52, R55, R56, R59, R60, R66, R68, R71, R72, R75, R76, R78, R79 | R2512 | C309607
0402WGF1002TCE | R35, R36, R37, R38, R40, R41, R42, R43 | R0402 | C25744
RC0402FR-0730RL | R67 | R0402 | C138007
0402WGF499JTCE | R80A, R80B, R82A, R82B | R0402 | C25120
HP03W5F1001T5E | R81A, R81B | R0603 | C2759450
SM91502ALA-E | T1A, T1B | BOURNS_SM91502 | C5337144
BQ79616PAPRQ1 | U1 | TI_PAP0064F | C3682338

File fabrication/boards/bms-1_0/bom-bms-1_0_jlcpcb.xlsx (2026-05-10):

Manufacturer Part Number | Designator | Footprint | JLCPCB Part #
S8421-45R | BT1 | HOLDER_BATT_CR2032_HARWIN_S8421-45R | C5185176
CL10A106MA8NRNC | C1, C2, C85A, C85B, C85C, C145, C160, C168, C170 | C0603 | C96446
CL05B103KB5NNNC | C3, C11, C48A, C48B, C48C, C51A, C51B, C51C, C138, C148A, C148B, C150A, C150B, C150C, C151A, C151B, C151C, C154A, C154B, C154C, C155A, C155B, C155C, C156A, C156B, C156C, C157A, C157B, C157C, C188A, C188B, C188C, C188D, C199A, C199B | C0402 | C15195
CL05B104KB54PNC | C4, C5, C6, C7, C8, C9, C10, C19, C24, C26, C30, C32, C37, C43, C45, C47A, C47B, C47C, C50A, C50B, C50C, C52A, C52B, C52C, C52D, C52E, C52F, C54A, C54B, C54C, C54D, C54E, C54F, C57A, C57B, C57C, C57D, C57E, C57F, C63, C64, C65, C66, C67, C68, C69, C70, C82A, C82B, C82C, C84A, C84B, C84C, C91, C94, C95, C96, C100, C101A, C101B, C102A, C102B, C103A, C103B, C104, C105, C106, C107, C108, C109, C110, C112, C113, C114, C115, C116, C117, C118, C119, C120, C121, C122, C123, C124, C125, C126, C128, C129, C130, C131, C132, C133, C141, C142, C143, C144, C149A, C149B, C152A, C152B, C152C, C153A, C153B, C153C, C158, C159, C161, C164, C165, C166, C167, C169, C171, C172, C190, C191, C192, C193, C194, C201 | C0402 | C307331
GMK107AB7105KAHT | C12, C39, C40, C92, C200 | C0603 | C841050
CL21B106KAYQNNE | C13, C38, C41, C93, C111, C127, C146, C162, C163, C189, C197A, C197B, C198A, C198B, C202 | C0805 | C3039694
0402CG270J500NT | C14, C34, C35, C36, C77, C137, C147, C195, C196 | C0402 | C1557
0402CG6R0C500NT | C15, C16, C78, C79, C135, C136, C139, C140 | C0402 | C1575
0402CG150J500NT | C17, C18 | C0402 | C1548
0805B475K500NT | C20, C27, C81A, C81B, C81C, C83A, C83B, C83C | C0805 | C2991173
CL21B106KOQNNNE | C21 | C0805 | C95841
C4532X7R1C336MT000N | C22, C28, C31 | C1812 | C342604
C5750X7R1E226MT000N | C23 | C2220 | C76694
CC0402KRX7R0BB222 | C25, C29, C33, C49A, C49B, C49C | C0402 | C576731
C5750X7T2E225KT000N | C42, C44, C46, C99 | C2220 | C435266
GCM21B5C2E472JX01L | C58, C61 | C0805 | C415370
GRM21B5C2E103JWAAL | C59, C62, C175, C176, C177 | C0805 | C3870620
EKXJ221ELL221MM25S | C60 | CAP_1600X2700X750 | C1600234
CL31B106KBHNNNE | C80 | C1206 | C89632
0402B473K500NT | C86A, C86B, C86C | C0402 | C82219
GRM1555C1H471JA01D | C87A, C87B, C87C | C0402 | C76971
FM31X104K251EEG | C88, C89 | C1206 | C365814
FM32X224K251EEG | C90 | C1210 | C146177
0402CG101J500NT | C98, C134 | C0402 | C1546
TMK105B7224KV-FR | C173, C174 | C0402 | C841047
GRM1555C1H221JA01D | C178, C179 | C0402 | C71693
XL-3528RGBW-HM | D1 | LED_RGB_SMD3528-4P | C2843813
PESD2USB3UX | D2, D15, D17 | 3SOT23 | C3708426
BAT54XV2T1G | D3, D10, D14, D35A, D35B, D35C, D36A, D36B, D36C, D38, D39 | SOD523 | C81572
SZMM5Z3V3T1G | D4 | SOD523 | C464127
LTST-C190YKT | D5, D18, D22A, D22B, D22C, D24 | LED_0603P_YELLOW | C125097
B340A-13-F | D6 | SMA | C85098
LTST-C191TBKT | D7 | LED_0603P_BLUE | C99290
MM3Z56VC | D9 | SOD323 | C891632
5.0SMDJ12A | D12 | SMC | C126819
30KPA120A | D13 | P600_VERTICAL | C1984717
MSS2P2-M3/89A | D16, D20A, D20B, D20C, D21A, D21B, D21C | ESMP | C2978531
LTST-C190KRKT | D19A, D19B, D19C, D32 | LED_0603P_RED | C94869
SBR10E45P5-7 | D23 | POWERDI5 | C73569
PESD2CAN,215 | D25A, D25B | 3SOT23 | C75176
LTST-C190GKT | D26, D28, D30, D33 | LED_0603P_GREEN | C125093
LTST-C190AKT | D27, D29, D31 | LED_0603P_AMBER | C6085129
BAT54SLT1G | D34A, D34B, D43A, D43B, D43C, D43D, D44A, D44B, D44C, D44D, D45 | 3SOT23 | C19726
PTVSLC3D3V3B | D42 | SOD323 | C246774
0ZRE0200FF1A | F3, F5 | BELFUSE_0ZRE0200FF | C3760983
BLM15AX601SN1D | FB1, FB3, FB4, FB11, FB12A, FB12B, FB13, FB15, FB16 | FB0402 | C76886
HCB2012KF-102T10 | FB5, FB7, FB9, FB10 | FB0805 | C356985
SMTSO-M3-2ET | H4, H5, H6, H14, H15, H16 | SMTSO-M3-2ET | C18212183
15115-91-0710 | H7, H8, H9, H10, H11, H12, H13 | PRECI-DIP_15115-91-0710 | C20239898
FTSH-107-01-L-DV-K-A | J1 | SAMTEC_FTSH-107-01-L-DV-K-A | C5563894
DM3BT-DSF-PEJS | J2 | HIROSE_DM3BT | C597972
XT30UPB-M | J7 | AMASS_XT30UPB-M | C428721
V8BR-1AX1-GH | J8 | BELFUSE_V8BR-1AX1-GH | C5346729
686108183822 | J9 | WURTH_WR-FPC_1.00mm_686108183822 | C2923676
UJ20-C-G-MSMT-TR-68 | J11 | CONN_USBC_UJ20-C-G-MSMT-TR-68 | C21943923
1-776163-1 | J12 | TE_AMPSEAL_1-776163-1 | C596198
1-776163-5 | J13 | TE_AMPSEAL_1-776163-5 | C17378321
RFPC-SMA14-FN-A | J14 | GCT_RFPC-SMA14-FN-A | C3173272
43650-0416 | J15 | MOLEX_MICROFIT_0436500416 | C587671
FTSH-105-01-L-DV-K | J16 | FTSH-105-01-L-DV-K_KEYED | C448647
LCB127STR | K4 | 6SMD300 | C6286119
CPC1150NTR | K5 | 4SMD300 | C5299824
FTC404020S4R7MGCA | L1, L2, L3 | SMD-4.1x4.1x2.0 | C39676072
LQW18AN68NJ80D | L4 | L0603_0.95MM | C269832
MMBT3906T | Q1 | 3SOT523 | C61615
S9013 | Q2, Q11A, Q11B, Q11C, Q11D | 3SOT23 | C431712
MMBT3904T | Q3, Q4, Q5, Q7 | 3SOT523 | C61616
FDC638P | Q6 | 6SOT23 | C241772
0402WGF330JTCE | R1, R2, R3, R4, R5, R6, R7, R9, R15, R16, R17, R18, R19, R21, R22, R23, R25, R26, R27, R28, R29, R31, R32, R33, R34, R35, R36, R37, R38, R40, R41, R43, R44, R45, R46, R47, R48, R49, R50, R51, R53, R56, R74, R95, R103, R120, R121, R123, R125, R128, R129, R131, R134, R149, R150, R151, R152, R153, R157, R158, R159, R161A, R161B, R172, R173, R174, R175, R178, R179, R190, R191, R192, R196, R197, R206, R207, R208, R210, R212, R213, R214, R228, R229, R230, R231, R232, R233, R243, R244, R247, R258, R259, R260, R261, R262, R263, R280, R282, R283, R284, R285, R286, R287, R290, R294 | R0402 | C25105
0402WGF3300TCE | R8, R12, R42, R55, R154, R181, R182, R186, R195, R219A, R219B, R219C, R227A, R227B, R227C, R251, R254, R275 | R0402 | C25104
0402WGF1001TCE | R10, R13, R14, R24, R39, R59, R61, R63, R72, R96, R104A, R104B, R104C, R104D, R104E, R104F, R107A, R107B, R107C, R107D, R107E, R107F, R132, R143A, R143B, R143C, R155, R156, R164, R165, R168, R169, R170, R171, R198, R200, R211, R223A, R223B, R223C, R224A, R224B, R224C, R225A, R225B, R225C, R226A, R226B, R226C, R248, R253, R266A, R266B, R266C, R266D, R292 | R0402 | C11702
CRCW04021R00FKED | R11, R78, R79, R166, R167, R199, R234, R241, R272, R281 | R0402 | C482087
ERJP06F1000V | R20, R205 | R0805 | C441975
0402WGF1002TCE | R30, R57, R58, R65, R66, R67, R68, R73, R75, R76, R81, R86, R93, R94, R110, R111, R114, R115, R116, R117, R136A, R136B, R136C, R137A, R137B, R137C, R140A, R140B, R140C, R144A, R144B, R144C, R146, R147, R148, R177, R183, R184, R185, R187, R188, R201, R209, R215, R239, R246, R249, R250, R255, R256, R257, R264A, R264B, R264C, R264D, R265A, R265B, R265C, R265D, R269, R270, R271, R273, R274, R276, R277, R278, R288, R289 | R0402 | C25744
0402WGF1501TCE | R52, R54, R204 | R0402 | C25867
0402WGF7322TCE | R60 | R0402 | C26986
HP05W3F220KT5E | R62 | R0805 | C2759317
0402WGF8872TCE | R64 | R0402 | C25922
0402WGF1003TCE | R69, R141A, R141B, R141C, R267, R268 | R0402 | C25741
0402WGF3302TCE | R70, R203 | R0402 | C25779
FRC0402F4532TS | R71 | R0402 | C2933099
0402WGF1004TCE | R77 | R0402 | C26083
WSL2726L5000FEB | R80, R83, R89 | VISHAY_WSL2726 | C4132421
TEH100M7R50FE | R82, R84 | TO-247-2_VERTICAL | C2641795
RC1206FR-072M2L | R85 | R1206 | C137329
0402WGF9531TCE | R87 | R0402 | C96273
0402WGF0000TCE | R88, R142A, R142B, R142C | R0402 | C17168
WSL27265L000FEB | R90, R160 | VISHAY_WSL2726 | C1517421
0402WGF750JTCE | R91A, R91B, R91C, R92A, R92B, R92C | R0402 | C25133
0402WGF3901TCE | R108 | R0402 | C51721
0402WGF4702TCE | R109, R113 | R0402 | C25792
TEH100M470RJE | R112 | TO-247-2_VERTICAL | C2642463
0402WGF4701TCE | R118, R119, R138A, R138B, R138C, R193, R194, R220A, R220B, R220C, R221A, R221B, R221C, R222A, R222B, R222C | R0402 | C25900
0402WGF2201TCE | R122, R124, R130, R133, R176, R180, R252 | R0402 | C25879
0402WGF5101TCE | R126, R127 | R0402 | C25905
FRC0402F10R0TS | R135A, R135B, R135C, R139A, R139B, R139C | R0402 | C2906862
HP06W2F130KT5E | R145A, R145B, R145C | R1206 | C414957
FRC0402F60R4TS | R162A, R162B, R163A, R163B | R0402 | C2960873
0402WGF6041TCE | R189 | R0402 | C25913
RC0402FR-07100RL | R202 | R0402 | C106232
0402WGF3301TCE | R217A, R217B | R0402 | C25890
FRC0402F6651TS | R218A, R218B | R0402 | C2998056
1206W4F1002T5E | R235, R236 | R1206 | C17902
FRC1206F49R9TS | R237, R238 | R1206 | C2907389
1206W4F1003T5E | R240 | R1206 | C17900
0402WGF1242TCE | R242 | R0402 | C11692
RTT2510R0FTE | R245 | R2512 | C105071
0402WGF1202TCE | R279 | R0402 | C25752
0402WGF499JTCE | R291, R293 | R0402 | C25120
CHS-04TA | S1 | SWITCH_NIDEC_CHS-04TA | C2921610
TS-1092S-B3D2-G | S2, S3, S7 | SWITCH_TS-1092S-B3D2-G | C520860
CHS-01TA | S4 | SWITCH_NIDEC_CHS-01TA | C2921603
CHS-02TA | S6A, S6B | SWITCH_NIDEC_CHS-02TA | C2921606
H1102NL | T1A, T1B, T1C | EPCOS_LAN_MODULE | C18584
ACT45B-101-2P-TL003 | T3A, T3B | CHOKE_ACT45B-101-2P-TL003 | C88056
ACT1210D-131-2P-TL00 | T4, T5 | CHOKE_ACT1210D-131-2P-TL00 | C5547342
RH-5002 | TP1, TP2 | TP_RH-5002 | C5199802
RH-5000 | TP3, TP32, TP33, TP34, TP35, TP36, TP37, TP51, TP71, TP89, TP90 | TP_RH-5000 | C5277086
RH-5001 | TP39, TP41, TP43, TP45, TP46, TP47, TP48, TP52, TP72, TP79 | TP_RH-5001 | C5199801
STM32F429NIH6 | U1 | ST_TFBGA216 | C710318
TPS65263QRHBRQ1 | U2 | TI_RHB | C2073290
MCP3913A1T-E/SS | U3 | 28SSOP65 | C628828
LAN8670C2T-E/LMX | U7 | QFN50P500X500X90-32N | C20901523
MP6519GQ-Z | U8A, U8B, U8C | MP6519 | C2762181
BME280 | U9 | BOSCH_BME280 | C92489
TCAN1462VDRQ1 | U10A, U10B | 8SOIC150 | C7399456
KSZ8567RTXV-VAO | U11 | MICROCHIP_C04-418B_128TQFP_14X14_10X10EP | C5229516
STM32F103CBT6 | U12 | 48TQFP7 | C8304
VN9E30FTR | U13A, U13B, U13C | ST_ECOPACK_QFN50P600X600X90-32N | C29447350
SI8662BB-B-IS1 | U14 | 16SOIC150 | C430287
ROL-0505S | U15 | 4SIP | C22372006
TPS79933QDDCRQ1 | U16, U20A, U20B | 5SOT23 | C2865613
LC29HEAMD | U17 | QUECTEL_LC29H | C28453488
MCP1502T-25E/CHY | U18 | 6SOT23 | C3680051
USB2534I-1080AEN | U19 | QFN50P600X600X90-36N | C626674
ISM330DLC | U21 | ST_LGA-14L | C2943126
BQ79600PWRQ1 | U22 | TI_PW0016A | C2869947
67WR20KLF | VR1 | TT_67W | C6826039
XRCGB25M000F3A00R0 | X1, X4, X7 | 4_SMD_2.0X1.6MM | C467842
9HT10-32.768KEZF-T | X2 | XTAL_TXC_9HT10 | C5932452
ABLS2-4.000MHZ-D4Y-T | X3 | XTAL_HC49US_SMD | C5933228
ECS-80-8-33Q-JES-TR | X5 | 4_SMD_3.2X2.5MM | C5727442
7A-24.000MAAJ-T | X6 | XTAL_TXC_7A | C2450230
3568 | XF6 | FUSEHOLDER_KEYSTONE_3568 | C3206956

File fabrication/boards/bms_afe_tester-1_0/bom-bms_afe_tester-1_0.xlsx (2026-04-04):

Comment | Designator | Footprint | JLCPCB Part #
GCM188R70J225KE22D | C1, C2, C43A, C43B, C43C, C43D | C0603 | C126582
CL05B103KB5NNNC | C3, C11 | C0402 | C15195
CL05B104KB54PNC | C4, C5, C6, C7, C8, C9, C10, C19, C24, C26, C30, C32, C36, C42A, C42B, C42C, C42D, C44, C45, C46, C49, C50, C54A, C54B, C54C, C54D, C54E, C54F, C54G, C54H, C54I, C54J, C54K, C54L, C54M, C54N, C54O, C54P, C56 | C0402 | C307331
CL10B105KA8NNNC | C12, C41A, C41B, C41C, C41D, C41E, C41F, C41G, C41H, C41I, C41J, C41K, C41L, C41M, C41N, C41O, C41P, C47, C55A, C55B, C55C, C55D, C55E, C55F, C55G, C55H, C55I, C55J, C55K, C55L, C55M, C55N, C55O, C55P | C0603 | C29936
CC0805KKX7R5BB106 | C13, C48 | C0805 | C527225
CC0402JRNPO9BN270 | C14, C51 | C0402 | C107002
CC0402CRNPO9BN6R0 | C15, C16, C52, C53 | C0402 | C700515
CL21B475KAFNNNE | C20, C27 | C0805 | C98195
CL31B106KBHNNNE | C21, C80A, C80B | C1206 | C89632
C4532X7R1C336MT000N | C22, C28, C31 | C1812 | C342604
CGA9N3X7R1C476MT0Y0N | C23 | C2220 | C342293
GRM1555C1H222GA01D | C25, C29, C33 | C0402 | C2987940
CL05C331JB5NNNC | C34A, C34B, C35A, C35B | C0402 | C13533
TAJB476M010RNJ | C37A, C37B, C37C, C37D, C37E, C37F, C37G, C37H, C37I, C37J, C37K, C37L, C37M, C37N, C37O, C37P, C39A, C39B, C39C, C39D, C39E, C39F, C39G, C39H, C39I, C39J, C39K, C39L, C39M, C39N, C39O, C39P | TANT_3.5MMX2.8MMX1.9MM | C8021
CGA3EAC0G2A103JT000E | C38A, C38B, C38C, C38D, C38E, C38F, C38G, C38H, C38I, C38J, C38K, C38L, C38M, C38N, C38O, C38P | C0603 | C342796
CL31B106KOHNNNE | C40A, C40B, C40C, C40D, C40E, C40F, C40G, C40H, C40I, C40J, C40K, C40L, C40M, C40N, C40O, C40P | C1206 | C47971
XL-3528RGBW-HM | D1 | LED_RGB_SMD3528-4P | C2843813
B340A-13-F | D2, D4A, D4B, D4C, D4D, D4E, D4F, D4G, D4H, D4I, D4J, D4K, D4L, D4M, D4N, D4O, D4P, D7A, D7B, D7C, D7D, D7E, D7F, D7G, D7H, D7I, D7J, D7K, D7L, D7M, D7N, D7O, D7P | SMA | C85098
PMEG10010ELR-QX | D3A, D3B, D3C, D3D, D3E, D3F, D3G, D3H, D3I, D3J, D3K, D3L, D3M, D3N, D3O, D3P | SOD123W | C5361358
LTST-C190YKT | D6 | LED_0603P_YELLOW | C125097
MM3Z15VC | D9 | SOD323 | C891582
PESD2USB3UX | D17A, D17B | 3SOT23 | C3708426
BLM15PX601SN1D | FB1, FB3 | FB0402 | C160977
MPZ2012S102AT000 | FB2 | FB0805 | C76817
SMTSO-M2-10ET | H1, H2, H3, H4, H5, H6, H7, H8, H9, H10, H11, H12, H13, H14, H15, H16, H17, H18, H19, H20, H21, H22, H23, H24, H25, H26, H27, H28, H29, H30, H31, H32 | SMTSO-M2-10ET | C2928171
FTSH-107-01-L-DV-K-A | J1 | SAMTEC_FTSH-107-01-L-DV-K-A | C5563894
0826-1L1T-57-F | J2 | BELFUSE_0826-1L1T-57-F | C3179913
TYPE-C-31-M-12 | J11A, J11B | CONN_USBC_TYPE-C-31-M-12 | C165948
FTC404020S4R7MGCA | L1, L2, L3 | SMD-4.1x4.1x2.0 | C39676072
IRLML0060TRPBF | Q1A, Q1B, Q1C, Q1D, Q1E, Q1F, Q1G, Q1H, Q1I, Q1J, Q1K, Q1L, Q1M, Q1N, Q1O, Q1P | 3SOT23 | C67274
DMP6023LFGQ-13 | Q3 | DIODES_POWERDI3333-8 | C672173
0402WGF1001TCE | R1, R2, R7, R24, R39, R60, R96, R97 | R0402 | C11702
CRCW040233R0FKED | R3, R4, R5, R6, R22, R26, R32, R35, R36, R38, R40, R41, R69A, R69B, R69C, R69D, R81, R82, R91, R92, R93, R128A, R128B, R129A, R129B | R0402 | C242490
CRCW06034R70FKEAHP | R8A, R8B, R8C, R8D, R8E, R8F, R8G, R8H, R8I, R8J, R8K, R8L, R8M, R8N, R8O, R8P, R14A, R14B, R14C, R14D, R14E, R14F, R14G, R14H, R14I, R14J, R14K, R14L, R14M, R14N, R14O, R14P | R0603 | C313771
0402WGF9103TCE | R9, R78 | R0402 | C25800
ESR18EZPF2202 | R10A, R10B, R10C, R10D, R10E, R10F, R10G, R10H, R10I, R10J, R10K, R10L, R10M, R10N, R10O, R10P | R1206 | C2105413
CRCW04021R00FKEDC | R11, R84 | R0402 | C2077765
0402WGF5101TCE | R12A, R12B, R13A, R13B | R0402 | C25905
AR05FTC1000 | R20 | R0805 | C234699
0402WGF1002TCE | R30, R51, R56, R61, R62, R63, R64, R65, R74A, R74B, R74C, R74D, R75A, R75B, R75C, R75D, R77, R83, R95, R98 | R0402 | C25744
0402WGF3300TCE | R42, R85 | R0402 | C25104
0402WGF7322TCE | R48 | R0402 | C26986
HP05W3F220KT5E | R49 | R0805 | C2759317
0402WGF8872TCE | R50 | R0402 | C25922
0402WGF1501TCE | R52, R54 | R0402 | C25867
0402WGF1003TCE | R57, R76 | R0402 | C25741
0402WGF3302TCE | R58 | R0402 | C25779
FRC0402F4532TS | R59 | R0402 | C2933099
HP06W2F120KT5E | R66A, R66B, R66C, R66D, R66E, R66F, R66G, R66H, R66I, R66J, R66K, R66L, R66M, R66N, R66O, R66P | R1206 | C414958
0402WGF6491TCE | R67A, R67B, R67C, R67D, R67E, R67F, R67G, R67H, R67I, R67J, R67K, R67L, R67M, R67N, R67O, R67P | R0402 | C25916
RC0402FR-076K98L | R68A, R68B, R68C, R68D, R68E, R68F, R68G, R68H, R68I, R68J, R68K, R68L, R68M, R68N, R68O, R68P | R0402 | C137944
0402WGF0000TCE | R70A, R70B, R70C, R70D, R71A, R71B, R71C, R71D, R72A, R72B, R72C, R72D, R73A, R73B, R73C, R73D | R0402 | C17168
0402WGF6041TCE | R79, R80 | R0402 | C25913
RC0402FR-0712K1L | R86 | R0402 | C132157
0402WGF499JTCE | R87, R88, R89, R90 | R0402 | C25120
TS-1092S-B3D2-G | S2, S3 | SWITCH_TS-1092S-B3D2-G | C520860
PH9585.003NLT | T1A, T1B, T1C, T1D, T1E, T1F, T1G, T1H, T1I, T1J, T1K, T1L, T1M, T1N, T1O, T1P | PULSE_PH9585 | C17554365
RH-5002 | TP1, TP2 | TP_RH-5002 | C5199802
RH-5000 | TP3, TP4, TP6, TP8, TP10, TP12, TP14, TP16, TP18, TP20, TP22, TP24, TP26, TP28, TP30, TP32, TP33, TP35, TP36, TP37 | TP_RH-5000 | C5277086
RH-5001 | TP5, TP7, TP9, TP11, TP13, TP15, TP17, TP19, TP21, TP23, TP25, TP27, TP29, TP31, TP34, TP38, TP39, TP41, TP43, TP45 | TP_RH-5001 | C5199801
STM32F427VGT6 | U1 | 100TQFP14 | C117815
TPS65263QRHBRQ1 | U2 | TI_RHB | C2073290
GP82410 | U3A, U3B, U3C, U3D, U3E, U3F, U3G, U3H, U3I, U3J, U3K, U3L, U3M, U3N, U3O, U3P | 5SOT23 | C19626938
DAC43204RTER | U5A, U5B, U5C, U5D | 16QFN4 | C5215475
HUSB238A-BB001-QN16R | U6 | QFN50P300X300X90-16N | C24833806
LAN8742AI-CZ-TR | U7 | 24QFN4E | C153279
XRCGB25M000F3A00R0 | X1, X3 | 4_SMD_2.0X1.6MM | C467842

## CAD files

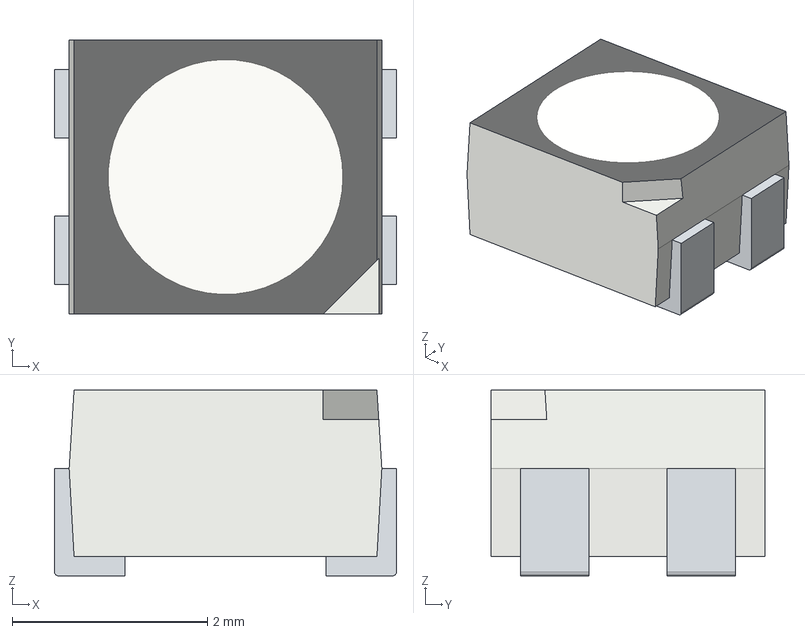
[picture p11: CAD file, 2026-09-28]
altium_library/footprints/common/XL-3528RGBW-HM.step
3.50 x 2.80 x 1.90 mm
XL-3528RGBW-HM housing and opaque diffuser
Pin 1 - Red cathode
Pin 2 - Common anode
Pin 3 - Green cathode
Pin 4 - Blue cathode

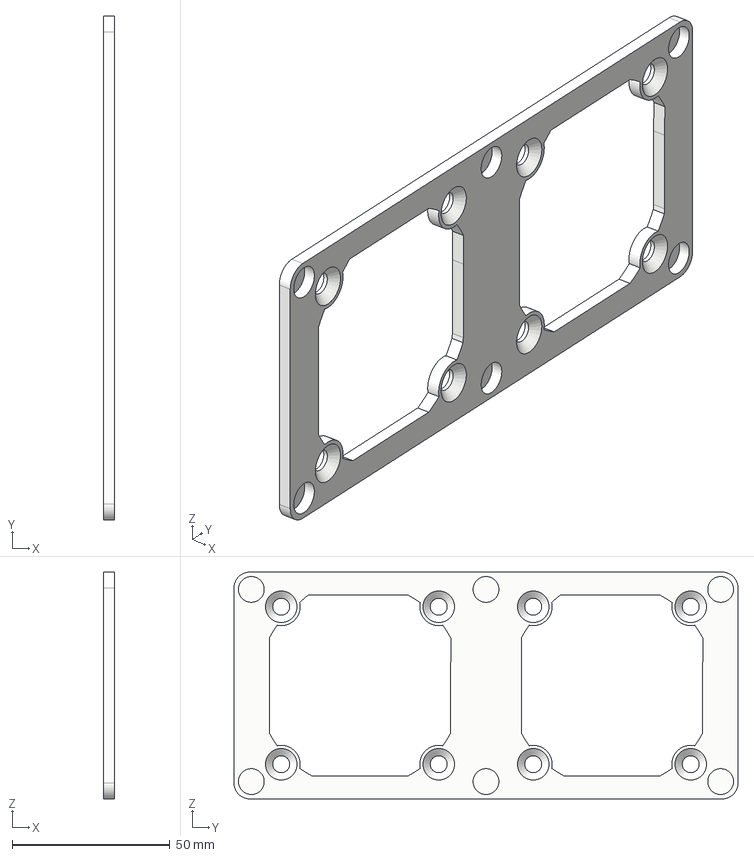
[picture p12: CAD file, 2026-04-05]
fabrication/parts_3dp/battery_box/exhaust_fan_mount.step
3.40 x 160.0 x 72.0 mm

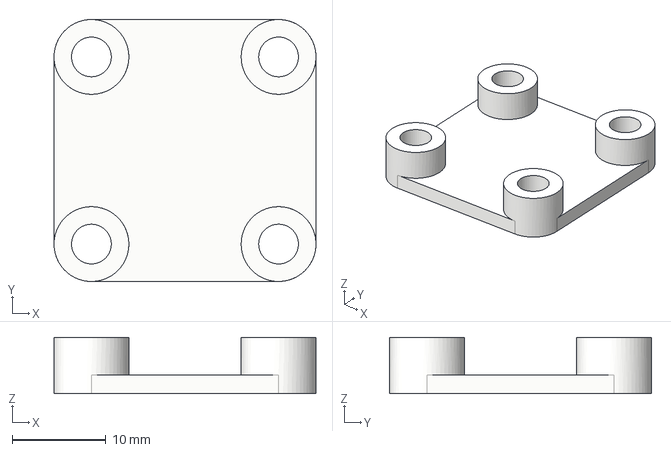
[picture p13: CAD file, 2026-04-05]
fabrication/parts_3dp/bms/bms_fan_adapter_mount.step
28.0 x 28.0 x 6.00 mm

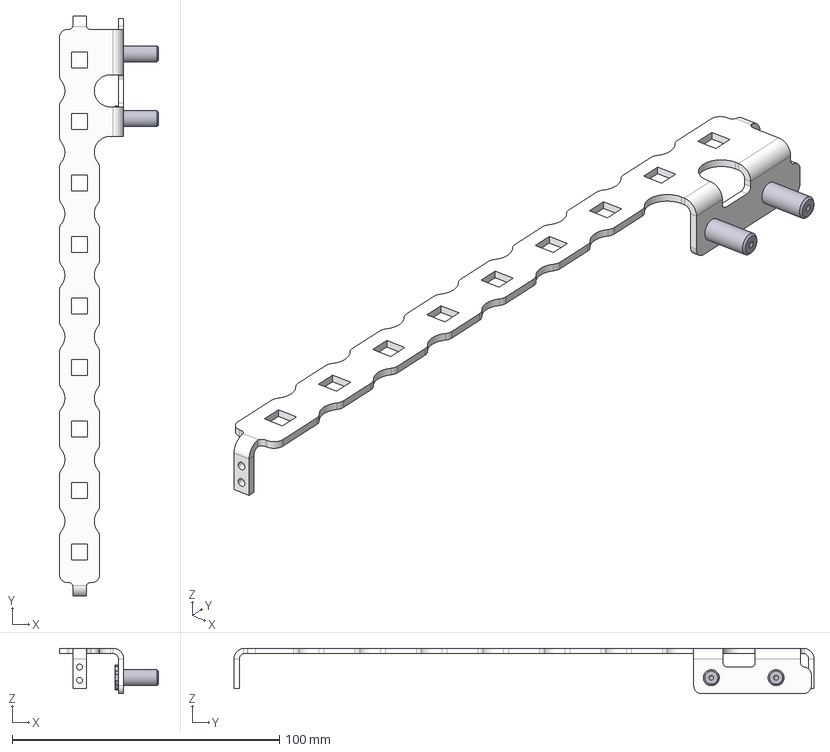
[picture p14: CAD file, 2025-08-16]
fabrication/parts_busbars/upper end collector.step
37.0 x 217.0 x 17.0 mm

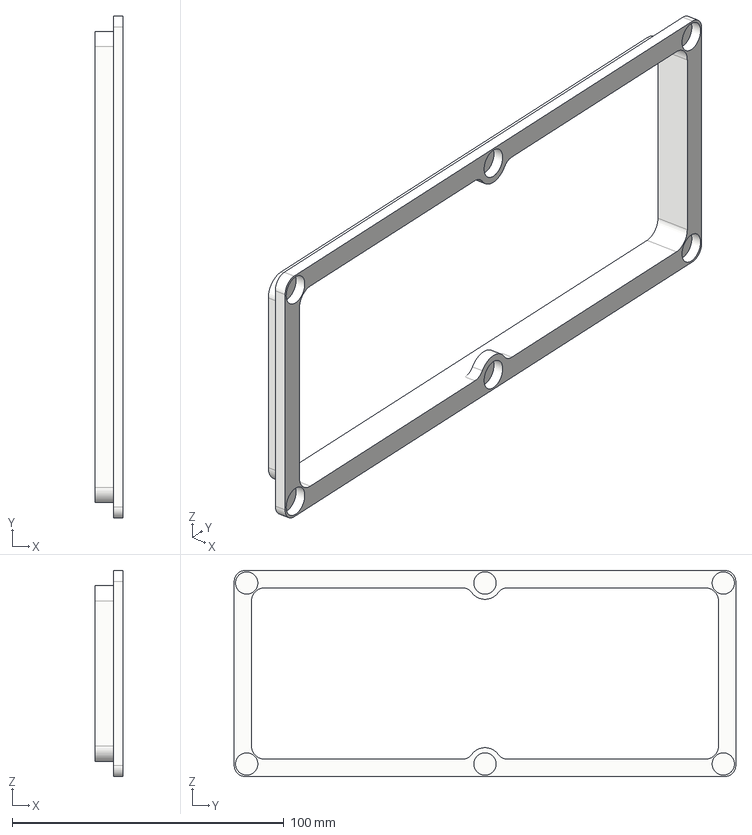
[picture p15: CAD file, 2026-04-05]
fabrication/parts_3dp/battery_box/intake_duct_collar.step
10.2 x 184.5 x 75.7 mm

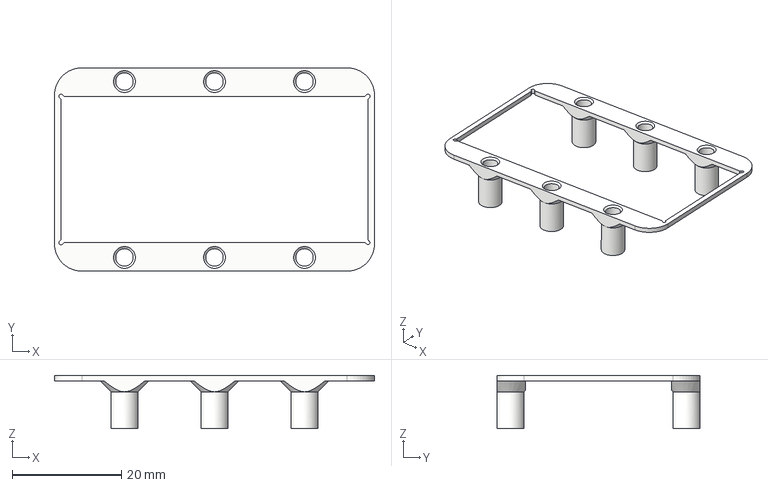
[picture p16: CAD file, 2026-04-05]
fabrication/parts_3dp/bms/vicor_mini_spacer.step
58.7 x 37.3 x 9.75 mm

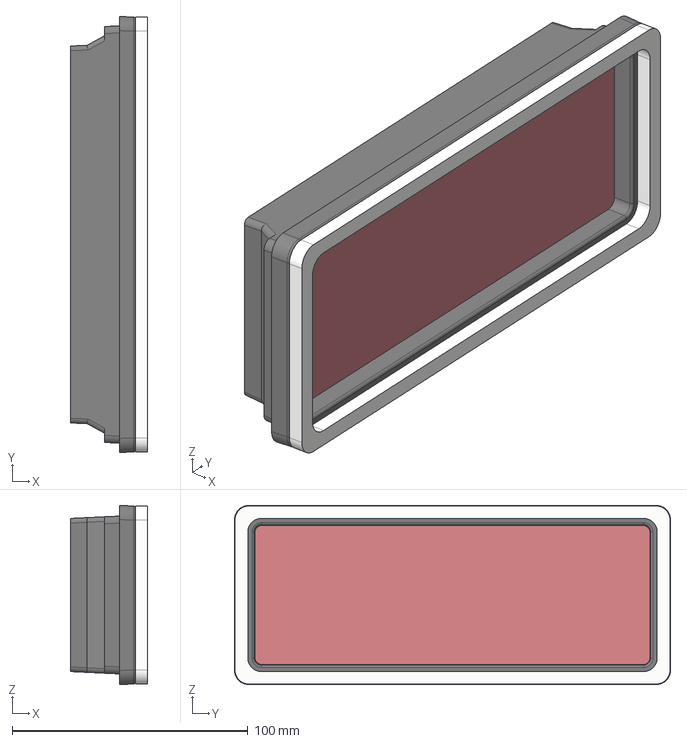
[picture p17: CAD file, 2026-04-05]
fabrication/parts_3dp/battery_box/intake_filter_mount.step
32.7 x 185.0 x 76.0 mm

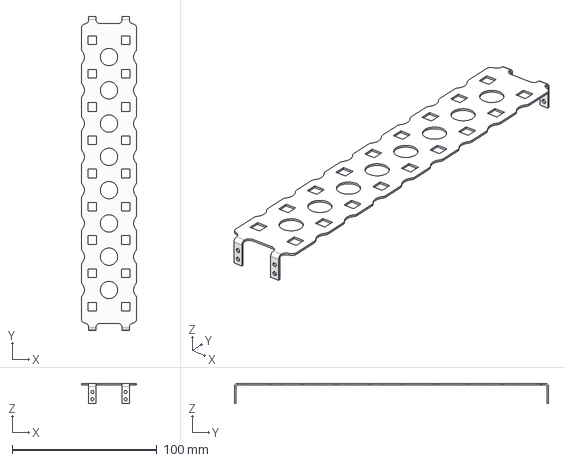
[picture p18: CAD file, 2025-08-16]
fabrication/parts_busbars/upper basic collector.step
38.0 x 217.0 x 14.0 mm

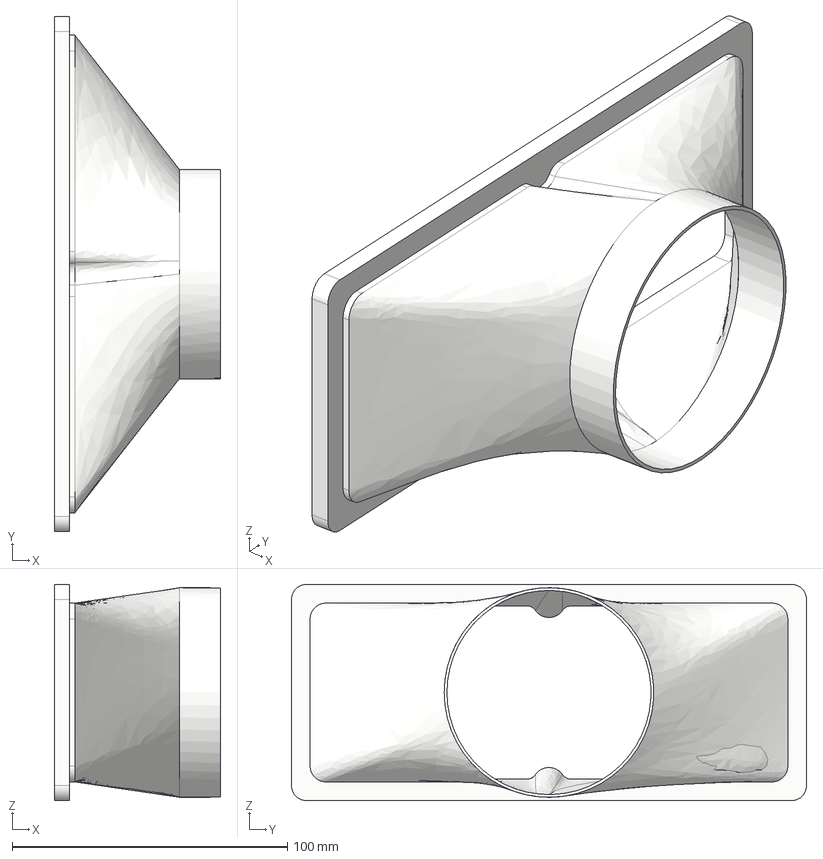
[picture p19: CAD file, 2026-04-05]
fabrication/parts_3dp/battery_box/intake_duct_adapter.step
60.4 x 187.3 x 78.5 mm

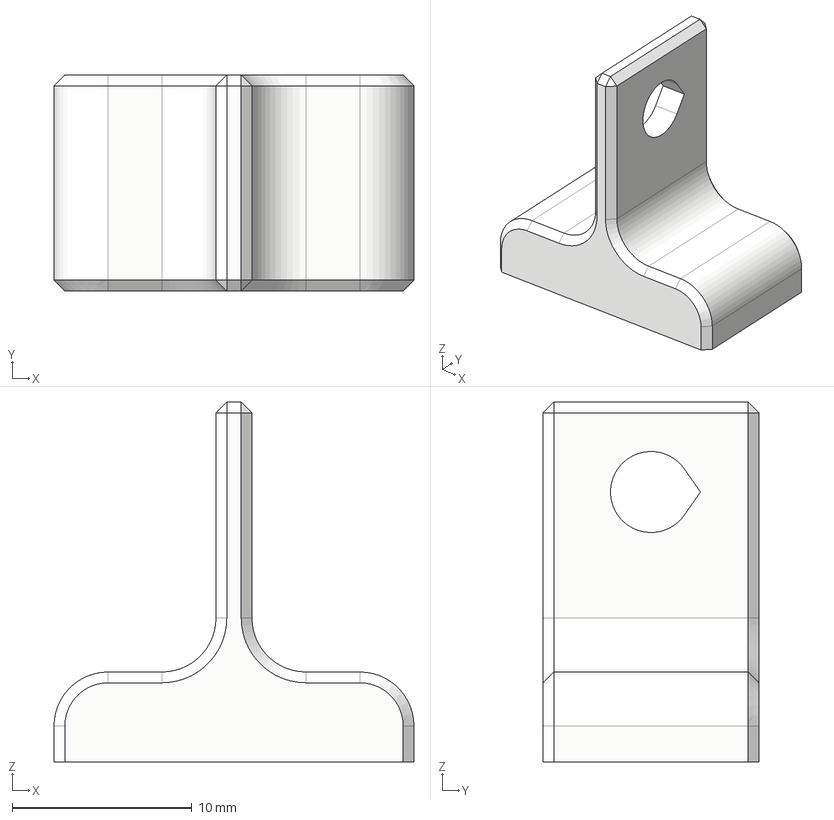
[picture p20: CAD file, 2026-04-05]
fabrication/parts_3dp/battery_box/hva280_cover_hasp.step
20.0 x 12.0 x 20.0 mm

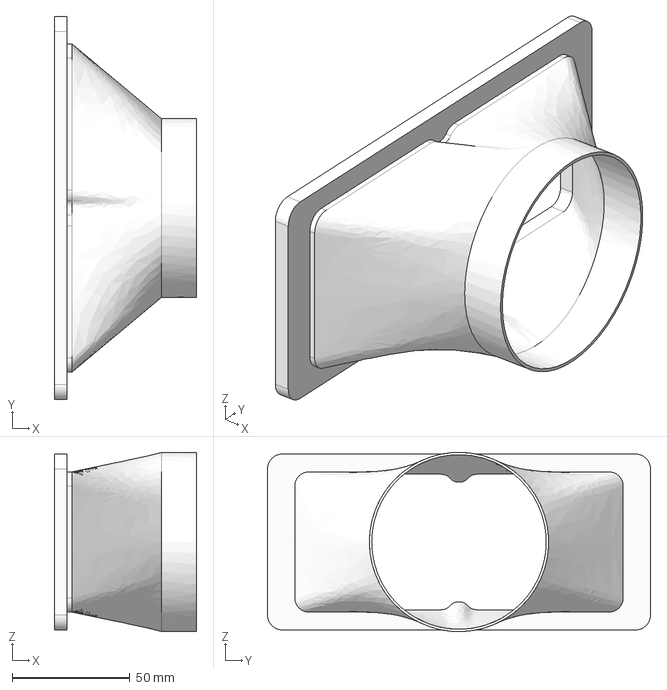
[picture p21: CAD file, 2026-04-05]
fabrication/parts_3dp/battery_box/exhaust_duct_adapter.step
60.4 x 162.8 x 76.2 mm

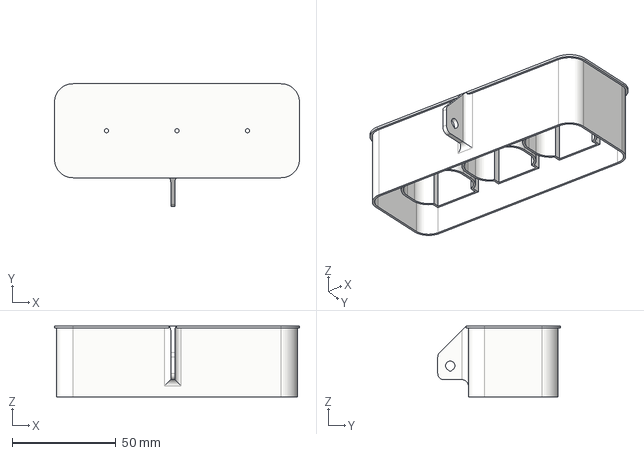
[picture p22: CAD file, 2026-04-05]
fabrication/parts_3dp/battery_box/hva280_cover.step
117.8 x 58.9 x 34.1 mm

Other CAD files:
fabrication/parts_busbars/upper end collector(Mirror).step

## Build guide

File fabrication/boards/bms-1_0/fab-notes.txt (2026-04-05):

Press-fit holes: J3, J21, J4, J5, J6, J18, J19, J20

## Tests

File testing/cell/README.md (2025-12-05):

# Motivation
Cells have varying incoming quality and we want to reject weak or bad cells. The pass/fail criteria will be left to the battery pack builder, but this script seeks to capture the data in time-efficient, semi-automated manner.

# Requirements
You will need:
* Pulse-capable Keithley source meter connected to your computer. I use a [Keithley 2430](https://www.tek.com/en/products/keithley/source-measure-units/2400-graphical-series-sourcemeter).
* 4-terminal battery chuck. I use [these, 15 amp flavor](https://a2delectronics.ca/shop/battery-testing/4-wire-cell-holder/).
* Barcode scanner. I have [this thing](https://www.amazon.com/dp/B01M264K5L).
* Serialized batteries
* Python 

# Workflow
All of the cells should be in thermal steady state in a temperature-controlled room prior to starting the test.
1. Launch the script.
2. Place a cell into the chuck.
3. Scan the barcode on the cell when prompted.
4. Wait for the tests to complete.
5. Place a new cell into the chuck and repeat until finished.

# Tests performed
The instrument is in four wire sensing mode. If the wires are shielded, the shield should be driven by the guard output of the instrument.
## Open circuit voltage
This is a very simple test. The source meter is placed in current-source mode with a zero current target, and the voltage at the terminals is measured over a short interval.
## R0 estimate
The cell voltage is measured with the cell idle (identical to the open circuit voltage test), and then again while sourcing a short high-current pulse. The dV/dI is the charging resistance. The tool then does this again, but discharging. This yields the discharging resistance. The average of the two is used as an estimate of the R0 impedance of the cell at the current state of charge. This should mostly be a measurement of the simple mechanical resistances and have little to do with the chemistry.
## DC impedance estimate
This test is similar to the R0 estimate, but uses a much longer pulse in order to try and get an estimate of the DC impedance. 

# Configurable parameters
Some constants defined at the top of the script can be tweaked to suit your particular cell parameters:
* _kChargeComplianceLimit_volts_ sets the upper voltage limit when sourcing current into the cell.
* _kDischargeCompianceLimit_volts_ sets the lower voltage limit when sinking current out of the cell.
* _kR0PulseCurrent_amps_ sets the pulse current used when estimating the R0 impedance of the cell.
* _kR0PulseDuration_seconds_ sets the length of the pulse when testing the R0 impedance of the cell.
* _kDcirPulseCurrent_amps_ sets the pulse current used when estimating the DC impedance of the cell.
* _kDcirPulseDuration_seconds_ sets the length of the pulse when testing the DC impedance of the cell.
* _kLeakageDwellTime_seconds_ sets the time that the instrument will wait for the current to settle to determine the leakage of the cell.

# Handy links
* [Keithley 2400-series user's manual, including SCPI programming](https://download.tek.com/manual/2400S-900-01_K-Sep2011_User.pdf)
* [PyVisa, for connecting to the instrument](https://pyvisa.readthedocs.io/en/latest/)

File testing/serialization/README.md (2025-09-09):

# Cell serialization

A lot of cells go into a solar car sized battery pack. I wanted to be able to do incoming quality tests on them in order to know which cells to keep or reject, and then to have enough data to do a good job of putting together parallel groups. I used a label printer and QR codes so that I could use a  (handheld barcode scanner)[https://www.amazon.com/dp/B01M264K5L] to get their serial numbers at test time.

The serial numbers are based on box number, row letter, and column number so that I could quickly find a specific cell within my inventory when it became time to populate cells into modules.

Edit the file `generate_serials.py` to generate whatever serial numbers you need. Run it with:

```
python3 generate_serials.py > serial_labels.csv
```

This produces a CSV file which is easy to use for printing.

# Printing

I'm using a Brother QL-720NW label printer, which has been obsolete for years. A modern equivalent appears to be the [Brother QL820NWBC](https://www.brother-usa.com/products/ql820nwbc).

For labels, either the [DK1221](https://www.brother-usa.com/products/dk1221) or [DK2214](https://www.brother-usa.com/products/dk2214) seem like reasonable labels. I used a [knock-off version](https://www.amazon.com/dp/B08Q7VB3YZ) of the latter because it was available as a plastic film which I prefer over paper for durability and thinness.

Follow [this guide](https://support.brother.com/g/b/faqend.aspx?c=us&lang=en&prod=3600eus&faqid=faqp00001040_003) to put together a label using the [P-Touch Editor software](https://www.brother-usa.com/ptouch/ptouch-label-editor-software).

Of course there are many other ways to label the cells, including just a marker.

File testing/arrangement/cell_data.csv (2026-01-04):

Serial Number | OCV (V) | R0 (Ohm) | R0 Charge (Ohm) | R0 Discharge (Ohm) | DCIR (Ohm) | DCIR Charge (Ohm) | DCIR Discharge (Ohm)
1A01 | 3.560265 | 0.02673035 | 0.0218749 | 0.0315858 | 0.0726665 | 0.052376 | 0.092957
1A02 | 3.56083 | 0.02731105 | 0.022919 | 0.0317031 | 0.072483833 | 0.05278 | 0.092187667
1A03 | 3.56041 | 0.02698935 | 0.0226567 | 0.031322 | 0.071250167 | 0.051247333 | 0.091253
1A04 | 3.559165 | 0.0270771 | 0.0225673 | 0.0315869 | 0.071991333 | 0.051406333 | 0.092576333
1A05 | 3.560236 | 0.0271302 | 0.0229782 | 0.0312822 | 0.072567667 | 0.052250333 | 0.092885
1A07 | 3.56096 | 0.02656605 | 0.0222022 | 0.0309299 | 0.070974167 | 0.052039667 | 0.089908667
1A08 | 3.560699 | 0.0262893 | 0.0224955 | 0.0300831 | 0.070986667 | 0.052741333 | 0.089232
1A09 | 3.558728 | 0.02715875 | 0.023207 | 0.0311105 | 0.070801333 | 0.051867333 | 0.089735333
1A10 | 3.561004 | 0.02629225 | 0.0225244 | 0.0300601 | 0.070123667 | 0.050576333 | 0.089671
1A11 | 3.560452 | 0.0263001 | 0.0221362 | 0.030464 | 0.069666 | 0.050913333 | 0.088418667
1A12 | 3.560265 | 0.0258826 | 0.0221144 | 0.0296508 | 0.069359167 | 0.050712667 | 0.088005667
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

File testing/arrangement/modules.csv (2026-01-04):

Module ID | Serial Number | Cell DCIR (Ohm) | Module Parallel DCIR (Ohm)
4 | 1A01 | 0.072666 | 0.007561
22 | 1A02 | 0.072484 | 0.007560
5 | 1A03 | 0.071250 | 0.007547
17 | 1A04 | 0.071991 | 0.007555
3 | 1A05 | 0.072568 | 0.007561
27 | 1A07 | 0.070974 | 0.007544
13 | 1A08 | 0.070987 | 0.007544
19 | 1A09 | 0.070801 | 0.007543
20 | 1A10 | 0.070124 | 0.007543
3 | 1A11 | 0.069666 | 0.007561
21 | 1A12 | 0.069359 | 0.007544
12 | 1A13 | 0.069938 | 0.007551
26 | 1B01 | 0.068925 | 0.007549
16 | 1B02 | 0.069137 | 0.007548
29 | 1B03 | 0.070534 | 0.007541
7 | 1B04 | 0.067818 | 0.007543
27 | 1B05 | 0.069343 | 0.007544
14 | 1B06 | 0.068151 | 0.007548
21 | 1B07 | 0.070077 | 0.007544
29 | 1B08 | 0.069268 | 0.007541
11 | 1B09 | 0.069939 | 0.007553
28 | 1B10 | 0.069850 | 0.007544
17 | 1B11 | 0.069900 | 0.007555
31 | 1B12 | 0.070512 | 0.007560
18 | 1B13 | 0.070132 | 0.007543
17 | 1C01 | 0.069108 | 0.007555
9 | 1C02 | 0.068701 | 0.007543
26 | 1C03 | 0.068088 | 0.007549
3 | 1C04 | 0.068805 | 0.007561
2 | 1C05 | 0.069235 | 0.007561
13 | 1C06 | 0.068609 | 0.007544
4 | 1C07 | 0.068772 | 0.007561
7 | 1C08 | 0.068746 | 0.007543
5 | 1C09 | 0.069644 | 0.007547
24 | 1C10 | 0.068409 | 0.007544
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

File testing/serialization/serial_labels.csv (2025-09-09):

Box | Row | Column | Serial
1 | A | 01 | 1A01
1 | A | 02 | 1A02
1 | A | 03 | 1A03
1 | A | 04 | 1A04
1 | A | 05 | 1A05
1 | A | 06 | 1A06
1 | A | 07 | 1A07
1 | A | 08 | 1A08
1 | A | 09 | 1A09
1 | A | 10 | 1A10
1 | A | 11 | 1A11
1 | A | 12 | 1A12
1 | A | 13 | 1A13
1 | B | 01 | 1B01
1 | B | 02 | 1B02
1 | B | 03 | 1B03
1 | B | 04 | 1B04
1 | B | 05 | 1B05
1 | B | 06 | 1B06
1 | B | 07 | 1B07
1 | B | 08 | 1B08
1 | B | 09 | 1B09
1 | B | 10 | 1B10
1 | B | 11 | 1B11
1 | B | 12 | 1B12
1 | B | 13 | 1B13
1 | C | 01 | 1C01
1 | C | 02 | 1C02
1 | C | 03 | 1C03
1 | C | 04 | 1C04
1 | C | 05 | 1C05
1 | C | 06 | 1C06
1 | C | 07 | 1C07
1 | C | 08 | 1C08
1 | C | 09 | 1C09
1 | C | 10 | 1C10
1 | C | 11 | 1C11
1 | C | 12 | 1C12
1 | C | 13 | 1C13
1 | D | 01 | 1D01
1 | D | 02 | 1D02
1 | D | 03 | 1D03
1 | D | 04 | 1D04
1 | D | 05 | 1D05
1 | D | 06 | 1D06
1 | D | 07 | 1D07
1 | D | 08 | 1D08
1 | D | 09 | 1D09
1 | D | 10 | 1D10
1 | D | 11 | 1D11
1 | D | 12 | 1D12
1 | D | 13 | 1D13
1 | E | 01 | 1E01
1 | E | 02 | 1E02
1 | E | 03 | 1E03
1 | E | 04 | 1E04
1 | E | 05 | 1E05
1 | E | 06 | 1E06
1 | E | 07 | 1E07
1 | E | 08 | 1E08
1 | E | 09 | 1E09
1 | E | 10 | 1E10
1 | E | 11 | 1E11
1 | E | 12 | 1E12
1 | E | 13 | 1E13
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

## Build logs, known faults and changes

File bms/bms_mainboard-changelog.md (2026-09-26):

## Changes to consider for next revision
* Add e-paper interface for status indication.

## Changes completed from 1.0 --> 1.1
* Added P600_VERTICAL to the solid-connect rule.
* Added TO-247-2_VERTICAL to the solid-connect rule.
* Fixed swapped SWDIO and SWCLK on STM32F103.
* Connected TPS79933 GND pin to GND.
* Removed 33 ohm series resistors on USB-C connector.
* Changed 24 MHz crystal BOM item and matching capacitors due to stocking.
* Added LED to HV_nBLEED signal.
* Added pull-up to SCL in case future chips do clock stretching.
* Used 3P3 for MP6519 EN pull-up because EN gates VCC regulator.
* Connected GNSS receiver wake line.
* Removed blocking diode and pull up resistor on GNSS nRST.
* Reduced slip fit to press fit on Wurth M4 terminals.
* Updated BOM to switch from MCP3913 to MCP3914B.
* Eliminated "shunt filter" on voltage sense channel.
* Harmonized -3dB corner for voltage and current sensing.
* Nudged MP6519 circuits to avoid contactor fill ports.
* Added switched and buffered LVB divider to STM32 ADC input.
* Added PPS test point.
* Reversed DIP switch net numbering to match printed label on DIP switch.
* Adjusted RGB LED resistors to get better color intensity matching.
* Fixed LED4_1 and LED3_1 polarity on Ethernet switch.
* Added a reverse-polarity fuse-blowing schottky diode to LVB/GND.
* Added bus switch to onboard SWD and debug buses to avoid STM32F1 backfeed.
* Changed HV BLEED resistor to 1k to reduce NC SSR self-heating.
* Fixed mistake where pack shunt override went to the array channel.
* Switched to non-waterproof USB-C connector (external cover required).
* Transformer-coupled isoUART from BQ79600.
* Changed isoUART to 2-pin connector.
* Added second isoUART interface to implement fault-tolerant ring.
* Changed VREF to 2.5 volt precision regulator.
* Changed analog input dividers to 1:2 for 5 volt range on 2.5 volt reference.
* Migrated to STM32H5F5LJH7Q to improve power consumption and performance.
* Moved LV_PWM to a regular timer.
* Changed D12 (LV TVS) to 15 volt standoff.
* Changed D13 (HV TVS) to 132 volt standoff.
* Eliminated the HV-present indicator. In practice it turned out not-useful.
* Eliminated FPC fan header and breakout. Used PC-industry 4-pin fan header.
* Add SD card bypass cap and pull-ups.
* Switch from 25 MHz crystal to 16 MHz crystal on STM32H5.
* Use BQ25690 for LV battery charging.
* Switch Vicor Micro to Cincon 40 watt ECLB for improved efficiency.
* Adjusted optical SSR LED drive strengths upwards to cover more edge cases.
* Added TAS5720ATDAPRQ1 audio amplifier; powered from LV2.
* Fixed top sheet note about PWM fractions for precharge relay current targets.
* Added RTL8152B and connected it to port 5 on the Ethernet switch.
* Added diode-OR on GNSS receiver V_BCKP domain from coin cell and VCC.
* Reduced capacitance of GNSS receiver TVS.
* Increased base drive resistance on antenna bias switch.
* Separated center taps on Ethernet switch magnetic center taps.
* Reduce VN9E30F supply resistor to 150 ohms to match 3.3v recommendation.
* Fixed missing pull-up resistor for Ethernet switch interrupt pin.
* Increased package size for digital input current-limiting resistor.
* Added VN9E30F direct input GPIO connections.
* Updated triple-buck ENx divider to account for EN pin leakage.
* Added insulation monitoring circuit.
* Added unity gain buffers to MCP3914B voltage inputs to mitigate leakage.
* Updated LAN8670 to D0 stepping to resolve errata.

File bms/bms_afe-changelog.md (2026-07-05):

## Changes from 1.0 --> 1.1
* Changed to 2-pin right-angle Microfit comms connector.
* Switched from capacitive to magnetic comms coupling.
* Switched to LCSC-stocked thermistor connector.

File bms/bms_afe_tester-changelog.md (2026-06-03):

## Changes to consider from 1.1 --> 1.2

## Changes from 1.0 --> 1.1
* Reduced hole size and fix part number on SMTSO clone.
* Switched to STM32H563.
* Got rid of HUSB238A and used MCU UCPD1 peripheral instead.
* Switched away from programmable flybacks to isolated, buffered DACs.
* Switched away from triple buck to discrete bucks.

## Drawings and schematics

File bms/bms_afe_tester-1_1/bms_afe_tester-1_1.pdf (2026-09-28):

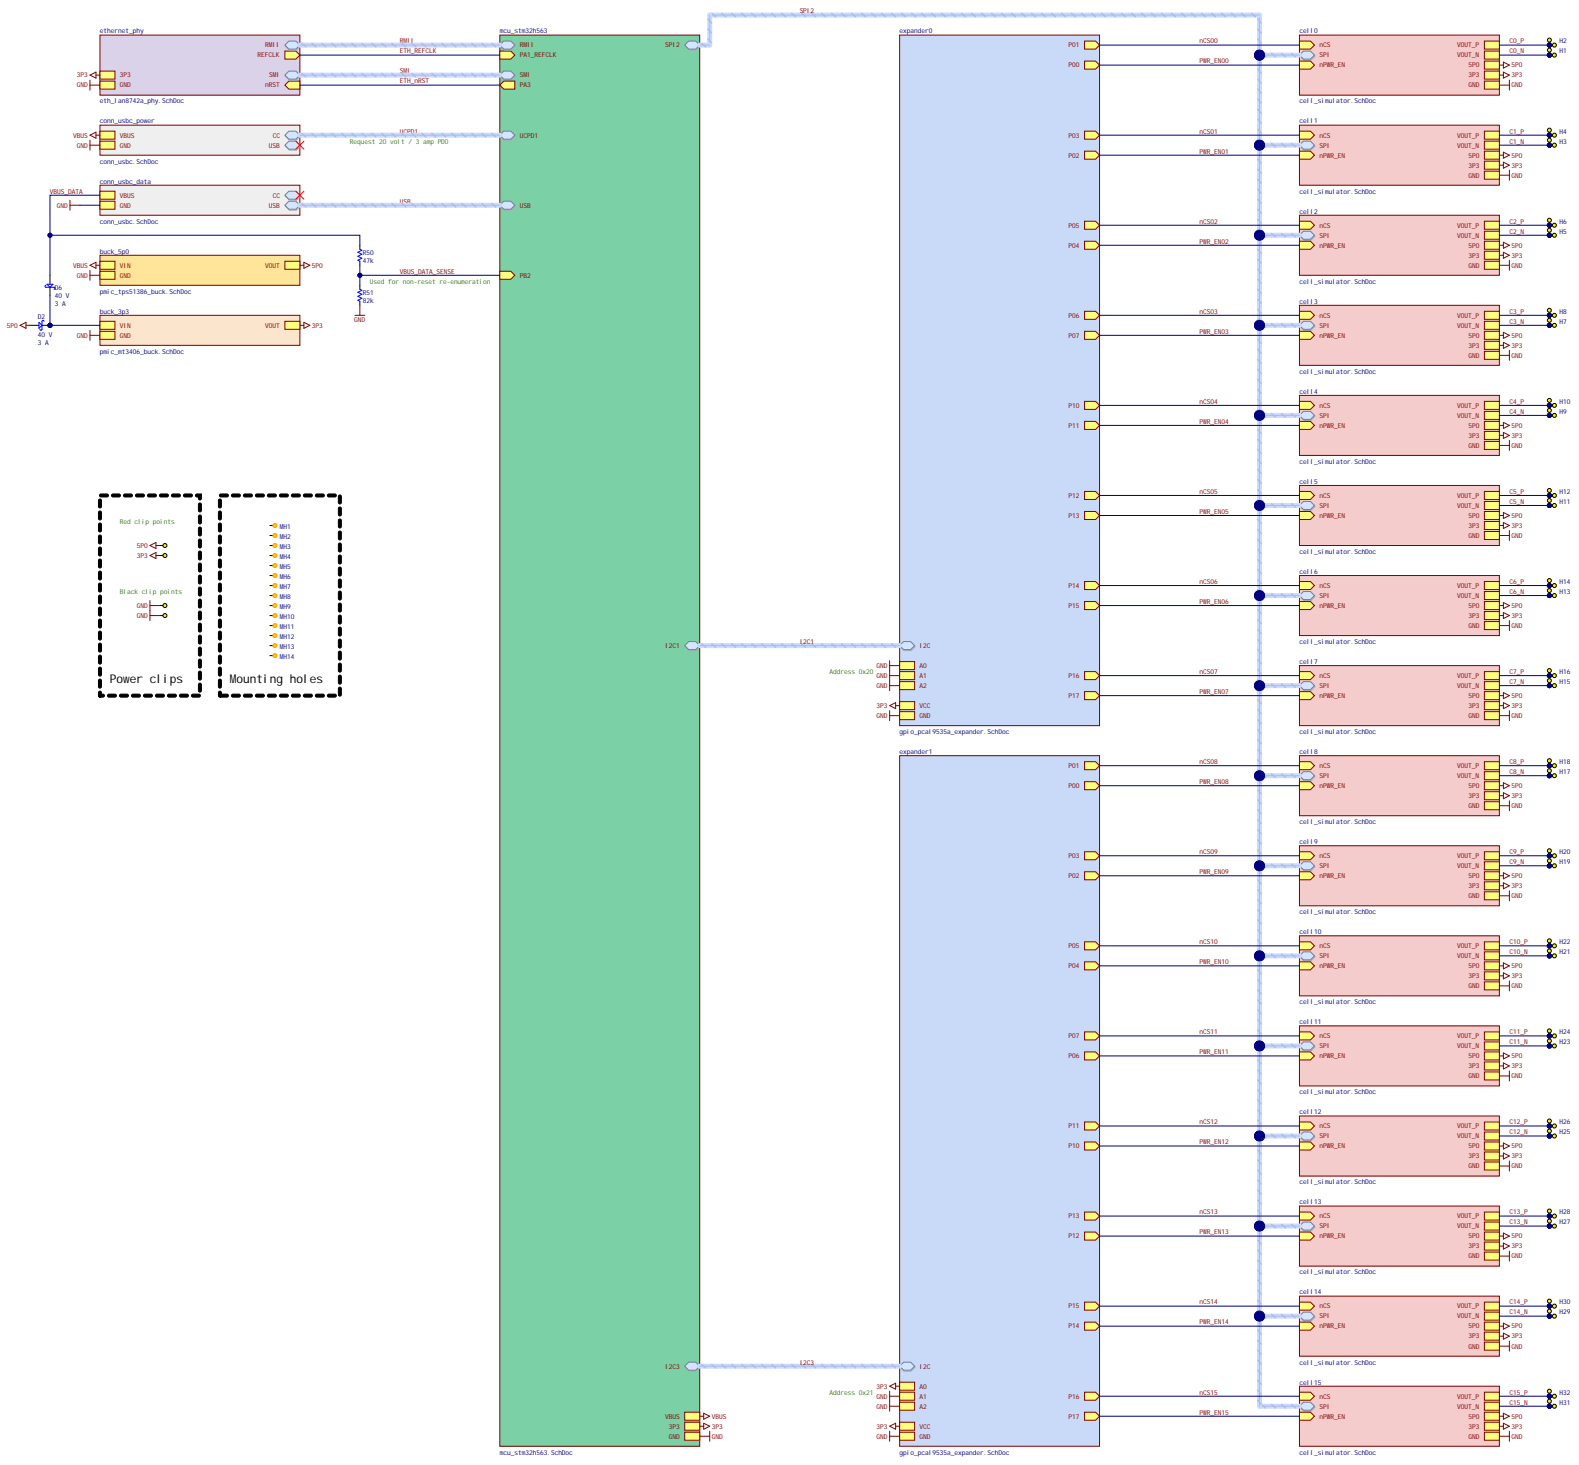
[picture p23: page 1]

Request 20 volt / 3 amp PDO

Used for non-reset re-enumeration

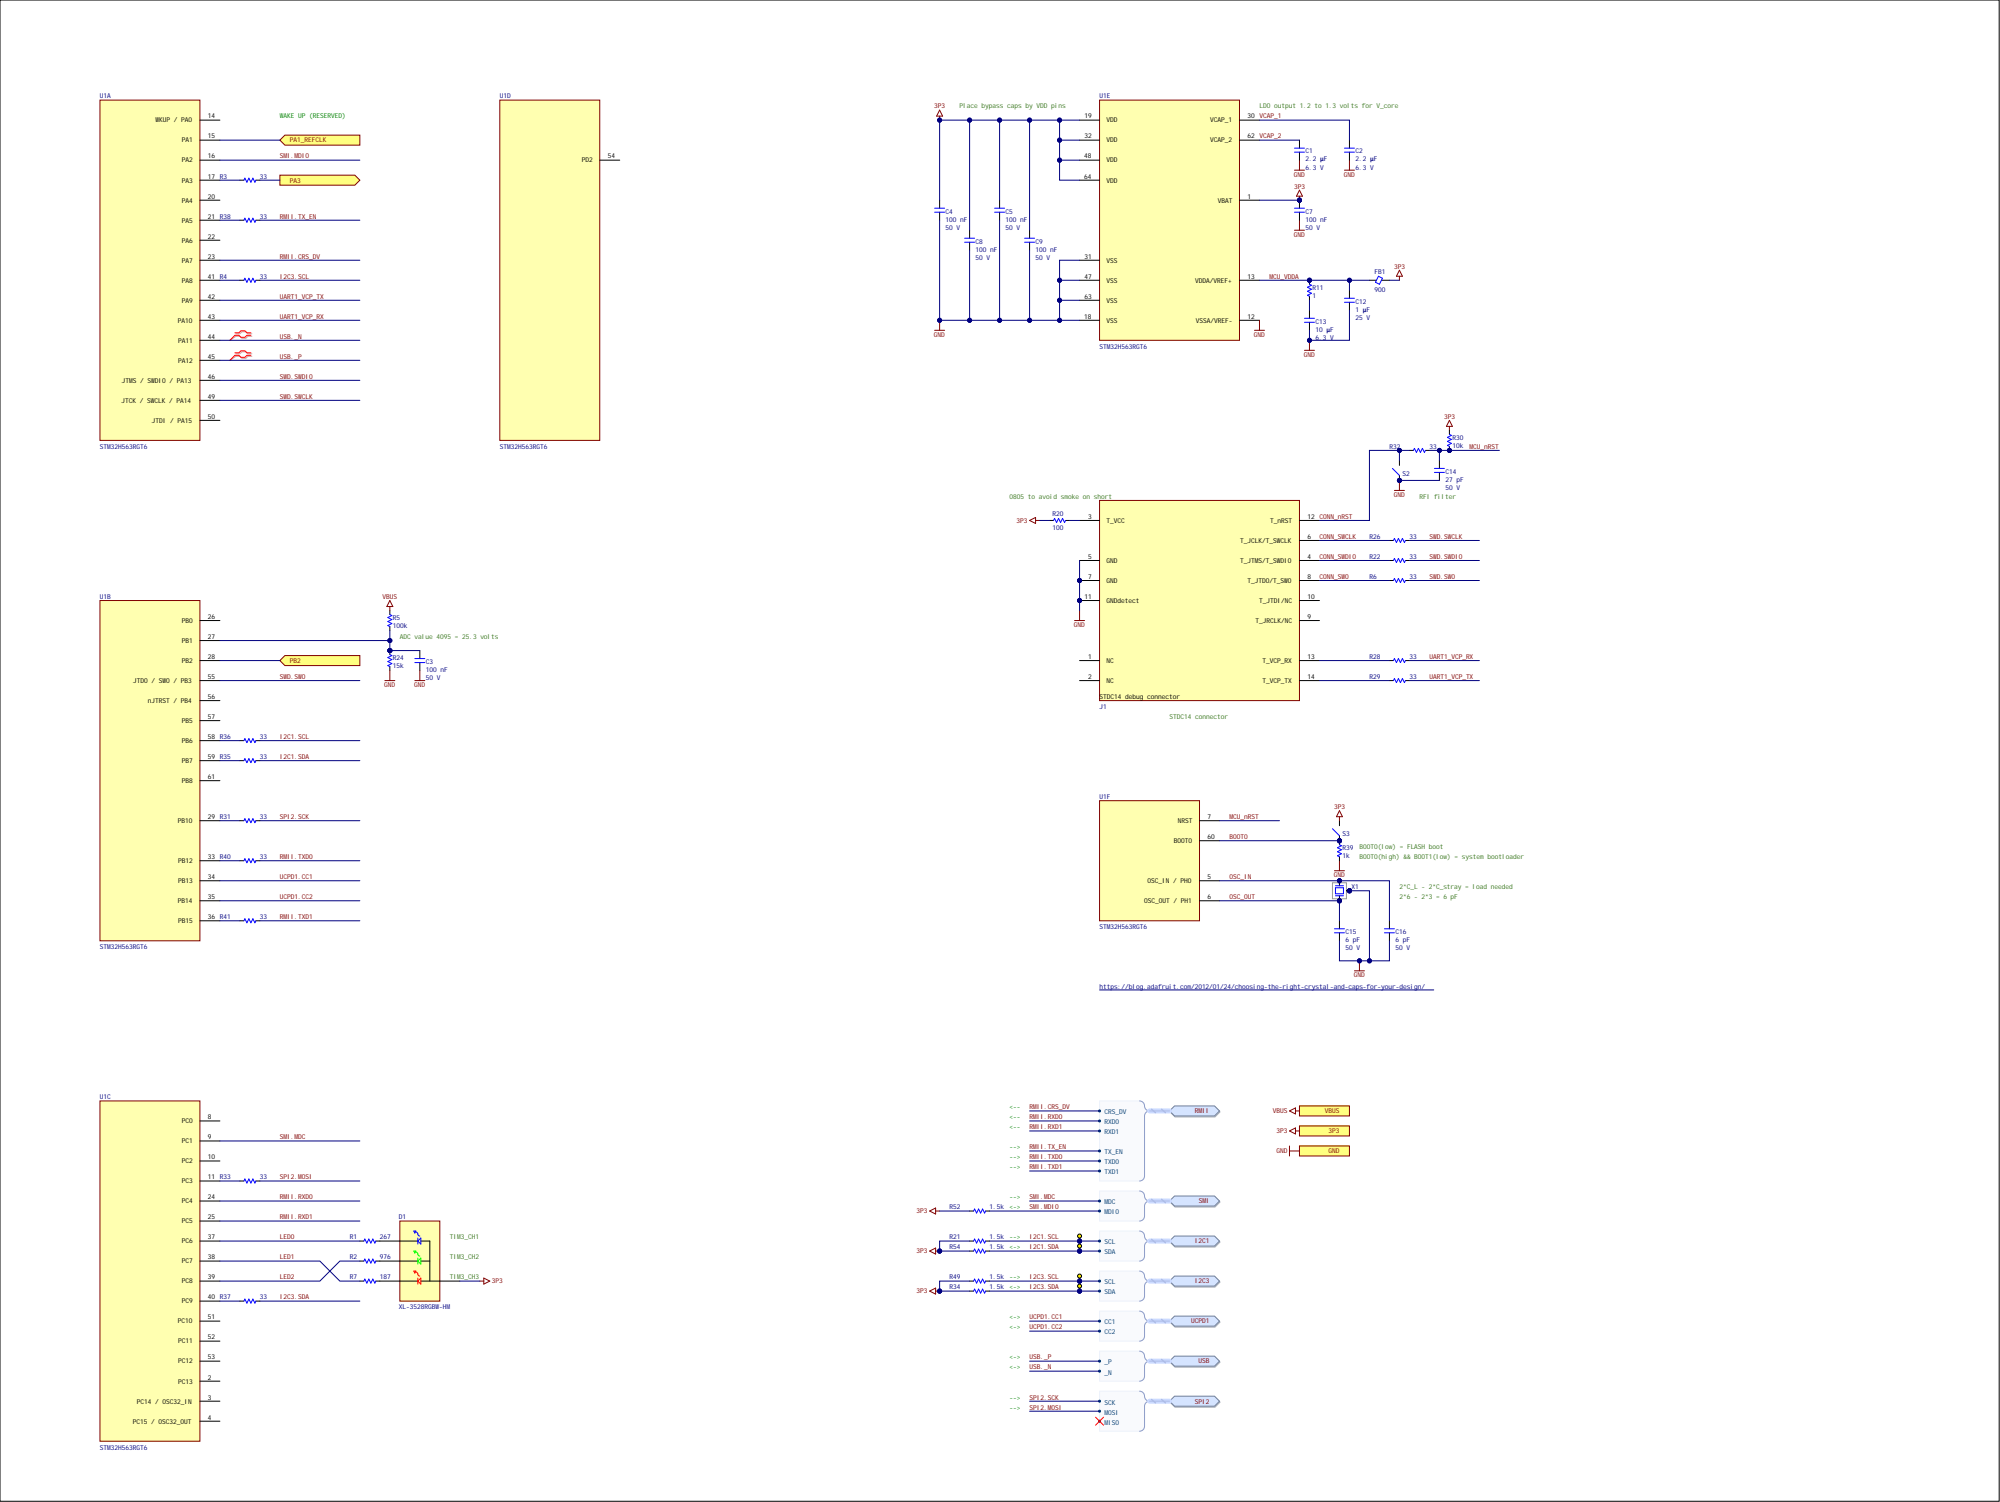
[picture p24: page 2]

Place bypass caps by VDD pins

LDO output 1.2 to 1.3 volts for V_core
VCAP_1

0805 to avoid smoke on short

https://blog.adafruit.com/2012/01/24/choosing-the-right-crystal-and-caps-for-your-design/

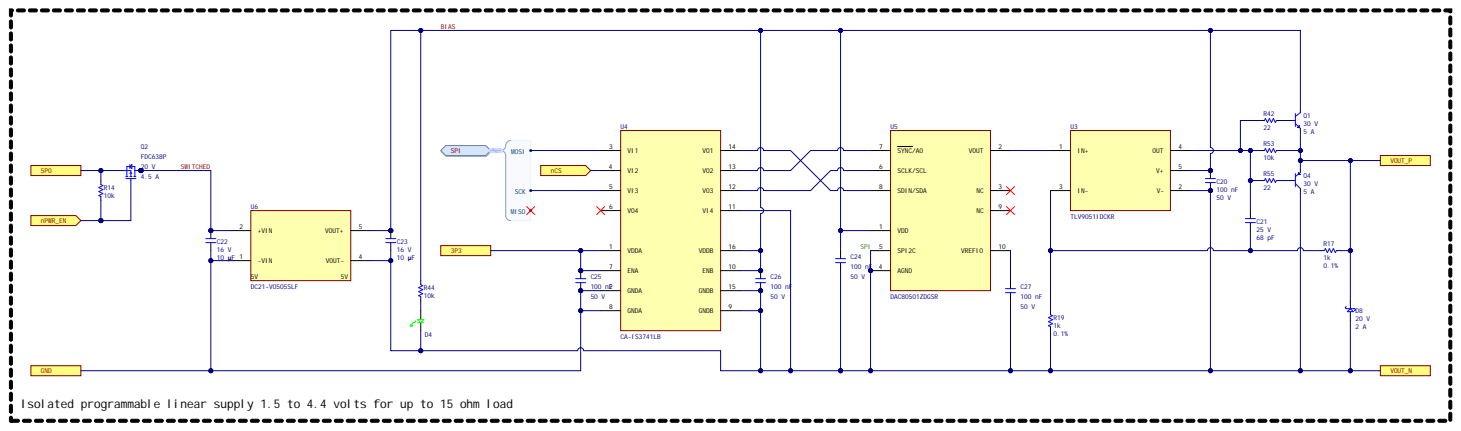
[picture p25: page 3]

Isolated programmable linear supply 1.5 to 4.4 volts for up to 15 ohm load

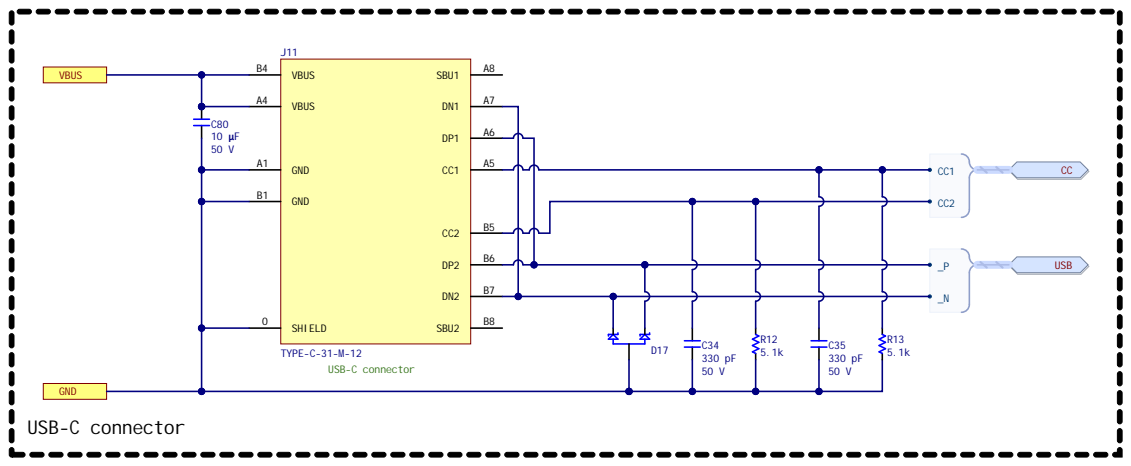
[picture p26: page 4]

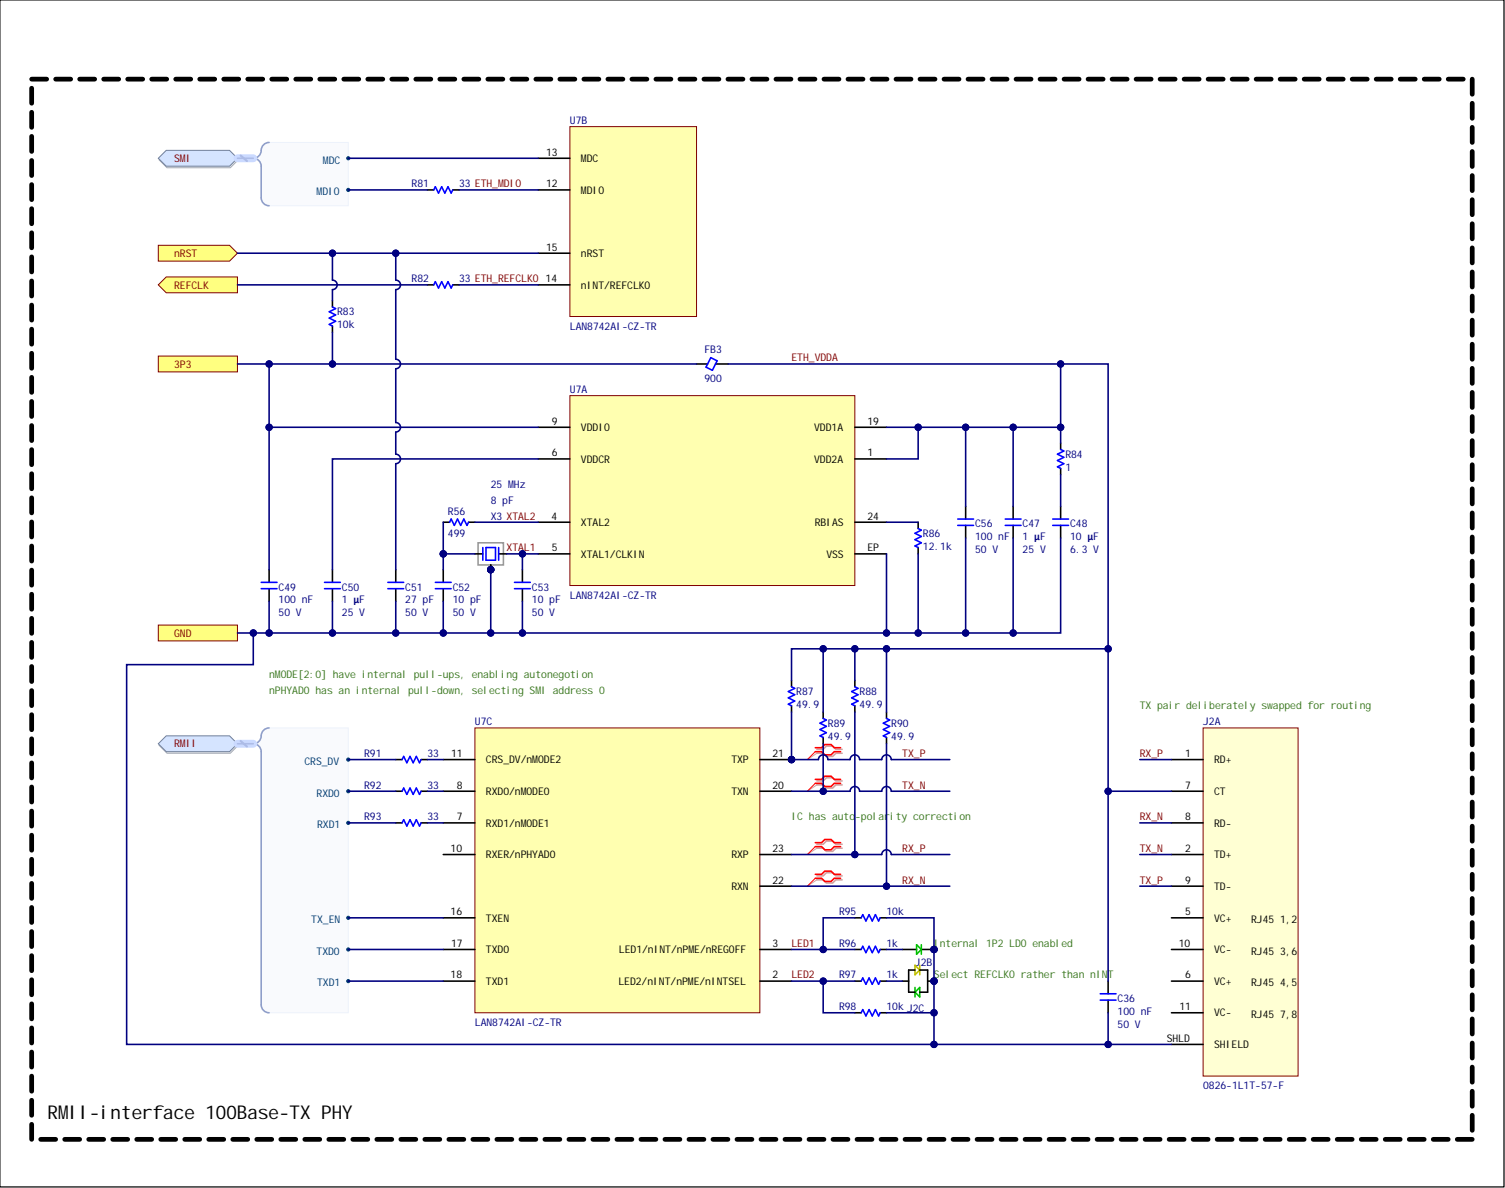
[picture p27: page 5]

25 MHz 8 pF R56 X3 XTAL2 | | XTAL2 4

XTAL1/CLKIN 5

nMODE[2:0] have internal pull-ups, enabling autonegotion
nPHYAD0 has an internal pull-down, selecting SMI address 0

TX pair deliberately swapped for routing

IC has auto-polarity correction

Internal 1P2 LDO enabled
Select REFCLKO rather than nINT

RMII-interface 100Base-TX PHY

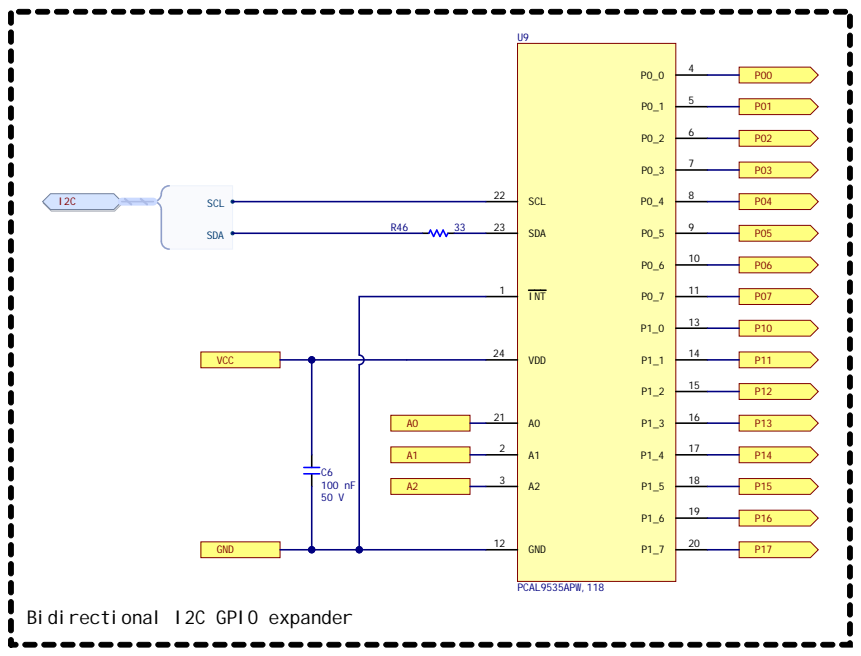
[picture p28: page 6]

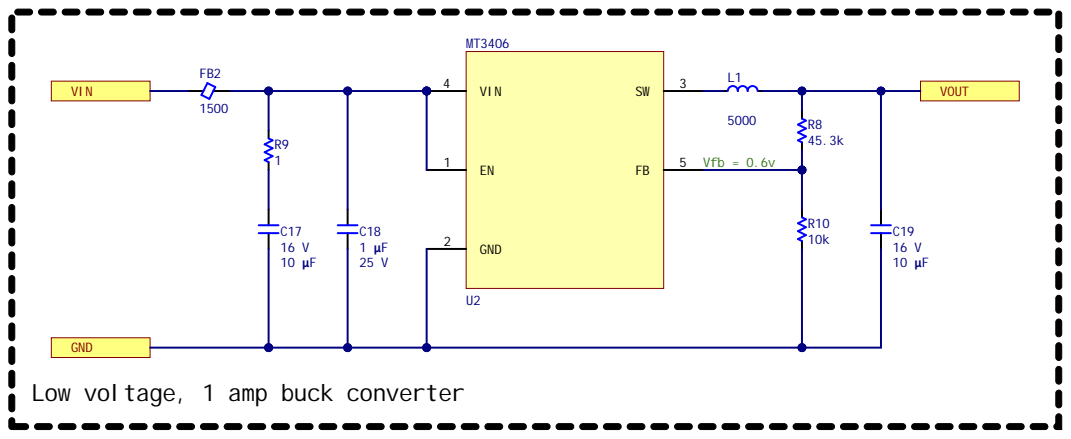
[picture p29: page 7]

GND
Low voltage, 1 amp buck converter

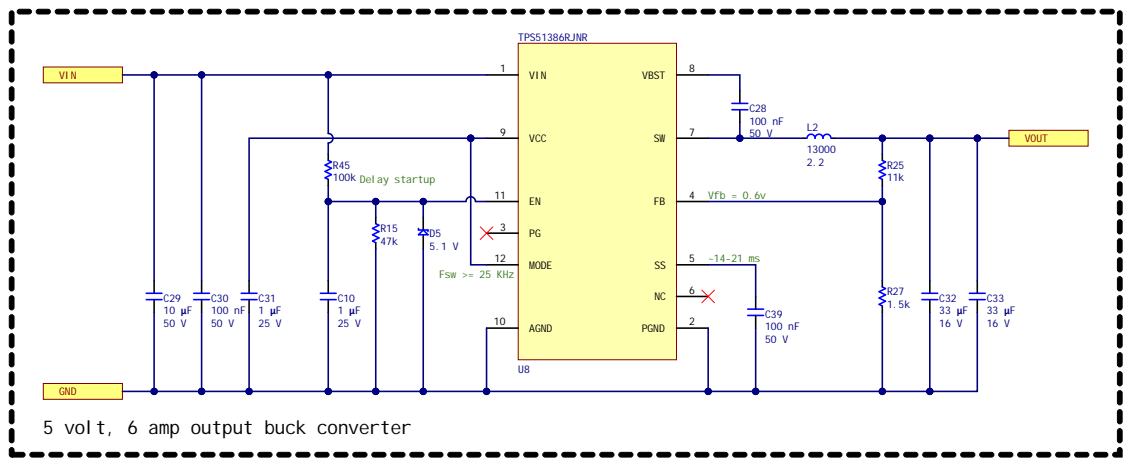
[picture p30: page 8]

R45 100k Delay startup | EN 11

GND
5 volt, 6 amp output buck converter

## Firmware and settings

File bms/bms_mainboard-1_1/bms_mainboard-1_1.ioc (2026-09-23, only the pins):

Mcu.UserName=STM32H5F5LJHxQ
PA0.GPIO_Label=FAN1_TACH
PA0.Signal=S_TIM2_CH1
PA1.GPIO_Label=ETH_REFCLK
PA1.Signal=ETH_RMII_REF_CLK
PA11.GPIO_Label=USB_DFP1_N
PA11.Signal=USB_OTG_FS_DM
PA12.GPIO_Label=USB_DFP1_P
PA12.Signal=USB_OTG_FS_DP
PA2.GPIO_Label=SMI_MDIO
PA2.Signal=ETH_MDIO
PA3.GPIO_Label=AIN0
PA3.Signal=ADCx_INP15
PA4.GPIO_Label=DAC1
PA4.Signal=COMP_DAC11_group
PA5.GPIO_Label=DAC2
PA5.Signal=COMP_DAC12_group
PA6.GPIO_Label=AIN1
PA6.Signal=ADCx_INP3
PA7.GPIO_Label=MCU_RMII_CRS_DV
PA7.Signal=ETH_RMII_CRS_DV
PA8.GPIO_Label=LV_PWM_CLK
PA8.Signal=S_TIM1_CH1
PB0.GPIO_Label=ADC_TP
PB0.Signal=ADCx_INP9
PB10.GPIO_Label=USART3_TX
PB10.Signal=USART3_TX
PB11.GPIO_Label=USART3_RX
PB11.Signal=USART3_RX
PB12.GPIO_Label=MCU_RMII_TXD0
PB12.Signal=ETH_RMII_TXD0
PB13.Signal=FDCAN2_TX
PB15.GPIO_Label=MCU_RMII_TXD1
PB15.Signal=ETH_RMII_TXD1
PB6.GPIO_Label=I2C1_SCL
PB6.Signal=I2C1_SCL
PB7.GPIO_Label=I2C1_SDA
PB7.Signal=I2C1_SDA
PB8.Signal=FDCAN1_RX
PB9.Signal=FDCAN1_TX
PC1.GPIO_Label=SMI_MDC
PC1.Signal=ETH_MDC
PC10.GPIO_Label=SDIO_D2
PC10.Signal=SDMMC1_D2
PC11.GPIO_Label=SDIO_D3
PC11.Signal=SDMMC1_D3
PC12.GPIO_Label=SDIO_CLK
PC12.Signal=SDMMC1_CK
PC14-OSC32_IN(OSC32_IN).GPIO_Label=LSE_IN
PC14-OSC32_IN(OSC32_IN).Signal=RCC_OSC32_IN
PC15-OSC32_OUT(OSC32_OUT).GPIO_Label=LSE_OUT
PC15-OSC32_OUT(OSC32_OUT).Signal=RCC_OSC32_OUT
PC3.GPIO_Label=LVB_DIV
PC3.Signal=ADCx_INP13
PC4.GPIO_Label=MCU_RMII_RXD0
PC4.Signal=ETH_RMII_RXD0
PC5.GPIO_Label=MCU_RMII_RXD1
PC5.Signal=ETH_RMII_RXD1
PC6.GPIO_Label=FAN1_PWM
PC6.Signal=S_TIM3_CH1
PC7.GPIO_Label=FAN2_PWM
PC7.Signal=S_TIM3_CH2
PC8.GPIO_Label=SDIO_D0
PC8.Signal=SDMMC1_D0
PC9.GPIO_Label=SDIO_D1
PC9.Signal=SDMMC1_D1
PD12.GPIO_Label=HS_CONTACTOR
PD12.Signal=S_TIM4_CH1
PD13.GPIO_Label=LS_CONTACTOR
PD13.Signal=S_TIM4_CH2
PD14.GPIO_Label=PRECHARGE_CONTACTOR
PD14.Signal=S_TIM4_CH3
PD2.GPIO_Label=SDIO_CMD
PD2.Signal=SDMMC1_CMD
PD3.GPIO_Label=IMU_INT1
PD3.Signal=GPXTI3
PD4.GPIO_Label=IMU_INT2
PD4.Signal=GPXTI4
PD5.GPIO_Label=USART2_TX
PD5.Signal=USART2_TX
PD6.GPIO_Label=USART2_RX
PD6.Signal=USART2_RX
PD9.Signal=FDCAN2_RX
PE0.GPIO_Label=UART8_RX
PE0.Signal=UART8_RX
PE1.GPIO_Label=UART8_TX
PE1.Signal=UART8_TX
PE10.GPIO_Label=MCP3913_nRST
PE10.Signal=GPIO_Output
PE11.GPIO_Label=SPI4_nSS
PE11.Signal=SPI4_NSS
PE12.GPIO_Label=SPI4_SCK
PE12.Signal=SPI4_SCK
PE13.GPIO_Label=SPI4_MISO
PE13.Signal=SPI4_MISO
PE14.GPIO_Label=SPI4_MOSI
PE14.Signal=SPI4_MOSI
PE15.GPIO_Label=MCP3913_nDR
PE15.Signal=GPXTI15
PE2.GPIO_Label=PMIC_FORCE_EN
PE2.Signal=GPIO_Output
PE3.GPIO_Label=PMIC_EN_DETECT
PE3.Signal=GPIO_Input
PE4.Signal=SAI1_FS_A
PE5.Signal=SAI1_SCK_A
PE6.Signal=SAI1_SD_A
PE7.GPIO_Label=UART7_RX
PE7.Signal=UART7_RX
PE8.GPIO_Label=UART7_TX
PE8.Signal=UART7_TX
PF14.GPIO_Label=HV_DCDC_EN
PF14.Signal=GPIO_Output
PF15.GPIO_Label=HV_nBLEED
PF15.Signal=GPIO_Output
PF6.GPIO_Label=EPAPER_SPI5_nSS
PF6.Signal=SPI5_NSS
PF7.GPIO_Label=EPAPER_SPI5_SCK
PF7.Signal=SPI5_SCK
PF8.GPIO_Label=EPAPER_SPI5_MISO
PF8.Signal=SPI5_MISO
PF9.GPIO_Label=EPAPER_SPI5_MOSI
PF9.Signal=SPI5_MOSI
PF13.GPIO_Label=IMD_EN_A
PF13.Signal=GPIO_Output
PG11.GPIO_Label=MCU_RMII_TX_EN
PG11.Signal=ETH_RMII_TX_EN
PG12.GPIO_Label=SPI6_MISO
PG12.Signal=SPI6_MISO
PG13.GPIO_Label=SPI6_SCK
PG13.Signal=SPI6_SCK
PG14.GPIO_Label=SPI6_MOSI
PG14.Signal=SPI6_MOSI
PG2.GPIO_Label=DIN0
PG2.Signal=GPIO_Input
PG3.GPIO_Label=DIN1
PG3.Signal=GPIO_Input
PG4.GPIO_Label=DIN2
PG4.Signal=GPIO_Input
PG5.GPIO_Label=DIN3
PG5.Signal=GPIO_Input
PG8.GPIO_Label=SPI6_nSS
PG8.Signal=SPI6_NSS
PH0-OSC_IN(PH0).GPIO_Label=HSE_IN
PH0-OSC_IN(PH0).Signal=RCC_OSC_IN
PH1-OSC_OUT(PH1).GPIO_Label=HSE_OUT
PH1-OSC_OUT(PH1).Signal=RCC_OSC_OUT
PH13.GPIO_Label=LV_nSS0
PH13.Signal=GPIO_Output
PH14.GPIO_Label=LV_nSS1
PH14.Signal=GPIO_Output
PH15.GPIO_Label=LV_nSS2
PH15.Signal=GPIO_Output
PH2.GPIO_Label=GNSS_nRST
PH2.Signal=GPIO_Output
PH3.GPIO_Label=GNSS_WAKEUP
PH3.Signal=GPIO_Output
PH6.GPIO_Label=TIMEPULSE
PH6.Signal=S_TIM12_CH1
PH9.GPIO_Label=ETH_SWITCH_SYNCLKO
PH9.Signal=S_TIM12_CH2
PI1.GPIO_Label=SPI2_SCK
PI1.Signal=SPI2_SCK
PI11.Signal=SAI1_MCLK_A
PI2.GPIO_Label=SPI2_MISO
PI2.Signal=SPI2_MISO
PI3.GPIO_Label=SPI2_MOSI
PI3.Signal=SPI2_MOSI
PI5.GPIO_Label=LED0_BLUE
PI5.Signal=S_TIM8_CH1
PI6.GPIO_Label=LED1_GREEN
PI6.Signal=S_TIM8_CH2
PI7.GPIO_Label=LED2_RED
PI7.Signal=S_TIM8_CH3
PI8.GPIO_Label=SPK_nSD
PI8.Signal=GPIO_Output
PI9.GPIO_Label=SPK_nFLT
PI9.Signal=GPIO_Input
PJ0.GPIO_Label=ETH_SWITCH_nSS3
PJ0.Signal=GPIO_Output
PJ1.GPIO_Label=ETH_SWITCH_nRST
PJ1.Signal=GPIO_Output
PJ13.GPIO_Label=SD_DETECT
PJ13.Signal=GPXTI13
PJ14.GPIO_Label=BQ25690_INT
PJ14.Signal=GPXTI14
PJ15.GPIO_Label=BQ25690_nCE
PJ15.Signal=GPIO_Output
PJ2.GPIO_Label=ETH_SW_nINT
PJ2.Signal=ETH_PHY_INTN
PJ3.GPIO_Label=LV0_DI0
PJ3.Signal=GPIO_Output
PJ4.GPIO_Label=LV0_DI1
PJ4.Signal=GPIO_Output
PJ5.GPIO_Label=LV1_DI0
PJ5.Signal=GPIO_Output
PJ6.GPIO_Label=LV1_DI1
PJ6.Signal=GPIO_Output
PJ7.GPIO_Label=FAN2_TACH
PJ7.Signal=S_TIM5_CH1
PJ8.GPIO_Label=LV2_DI0
PJ8.Signal=GPIO_Output
PJ9.GPIO_Label=LV2_DI1
PJ9.Signal=GPIO_Output
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

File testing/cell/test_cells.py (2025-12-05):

import argparse
import csv
import time
import sys
import string
import pyvisa

required_packages = {
    'pyvisa': 'pyvisa',
    'serial': 'pyserial'
}
missing_packages = []
for import_name, install_name in required_packages.items():
    try:
        __import__(import_name)
    except ImportError:
        missing_packages.append(install_name)

if missing_packages:
    print("\n\033[91mError: Missing required dependencies.\033[0m")
    print(f"The following packages are missing: {', '.join(missing_packages)}")
    sys.exit(1)

# Configurable parameters
kChargeComplianceLimit_volts = 4.2
kDischargeCompianceLimit_volts = 2.5
kR0PulseCurrent_amps = 10.0
kR0PulseDuration_seconds = 0.0025
kDcirCurrent_amps = 3.0
kDcirDuration_seconds = 10.0
kVoltageSenseDwell_seconds = 0.1

class Keithley2430:
    def __init__(self, resource_name, mock=False, terminals='front'):
        self.mock = mock
        if not self.mock:
            rm = pyvisa.ResourceManager()
            self.inst = rm.open_resource(
                resource_name,
                baud_rate=57600,
                data_bits=8,
                parity=pyvisa.constants.Parity.none,
                stop_bits=pyvisa.constants.StopBits.one,
                write_termination="\n",
                read_termination="\n",
                )
            self.inst.write("*RST")
            self.inst.write(":SYST:RSEN ON") # 4-wire mode
            
            # Select terminals
            if terminals.lower() == 'rear':
                self.inst.write(":ROUT:TERM REAR")
            else:
                self.inst.write(":ROUT:TERM FRONT")
        else:
            print(f"Mocking connection to {resource_name}")

    @staticmethod
    def CleanString(inputString):
        return "".join(filter(lambda x: x in string.printable, inputString))

    @staticmethod
    def ParseReading(inputString):
        cleanedString = Keithley2430.CleanString(inputString)
        splitString = cleanedString.split(',')
        dataDict = {'voltage': float(splitString[0]), \
                    'current': float(splitString[1]), \
                    'resistance': float(splitString[2]), \
                    'time': float(splitString[3]), \
                    'status': float(splitString[4])}
        return dataDict

    def close(self):
        if not self.mock:
            self.inst.write(":OUTP OFF")
            self.inst.close()

    def output_on(self):
        if not self.mock:
            self.inst.write(":OUTP ON")

    def output_off(self):
        if not self.mock:
            self.inst.write(":OUTP OFF")
    
    def beep_success(self):
        if not self.mock:
            self.inst.write("SYST:BEEP:IMM 1400, 0.1")
            time.sleep(0.1)
            self.inst.write("SYST:BEEP:IMM 2000, 0.05")
            time.sleep(0.05)

    def measure_voltage(self):
        if self.mock: return 3.7
        self.inst.write(":SOUR:FUNC:SHAP DC")
        # :READ? triggers a measurement based on current configuration
        return self.ParseReading(self.inst.query(":MEAS:VOLT?"))['voltage']

    def measure_current(self):
        if self.mock: return 0.0
        self.inst.write(":SOUR:FUNC:SHAP DC")
        return self.ParseReading(self.inst.query(":MEAS:CURR?"))['current']

    def source_current(self, current, voltage_limit):
        """Sets the source to current mode with a voltage compliance limit."""
        if not self.mock:
            self.inst.write(":SOUR:FUNC:SHAP DC")
            self.inst.write(":SOUR:FUNC CURR")
            self.inst.write(f":SOUR:CURR {current}")
            self.inst.write(f":SENS:VOLT:PROT {voltage_limit}")

    def source_voltage(self, voltage, current_limit):
        """Sets the source to voltage mode with a current compliance limit."""
        if not self.mock:
            self.inst.write(":SOUR:FUNC:SHAP DC")
            self.inst.write(":SOUR:FUNC VOLT")
            self.inst.write(f":SOUR:VOLT {voltage}")
            self.inst.write(f":SENS:CURR:PROT {current_limit}")

    def source_pulse_current(self, current, voltage_limit, width, delay=0):
        """Executes a current pulse and returns the measured voltage."""
        if self.mock:
            return 3.8 if current > 0 else 3.6 # Mock voltage rise/drop
        
        # Configure pulse mode
        self.inst.write(":SOUR:FUNC:SHAP PULS")
        self.inst.write(":SOUR:FUNC:MODE CURR")
        self.inst.write(":SENS:VOLT:RANG 20")
        self.inst.write(f":SOUR:CURR:LEV {current}")
        self.inst.write(f":SENS:VOLT:PROT {voltage_limit}")
        self.inst.write("SENS:FUNC \"VOLT\"")
        self.inst.write(f":SOUR:PULS:WIDT {width}")
        self.inst.write(f":SOUR:PULS:DEL {delay}")

        # Configure for one pulse
        self.inst.write(":TRIG:CLE")
        self.inst.write(":ARM:COUN 1")
        self.inst.write(":TRIG:COUN 1")
        
        # :READ? initiates the pulse sequence and returns the measurement.
        # Pulse mode automatically turns the output on and off.
        result = self.ParseReading(self.inst.query(":READ?"))['voltage']
        
        return result

    def test_connection(self):
        """Tests the connection to the instrument by querying its ID."""
        if self.mock:
            print("Mock connection successful.")
            return True
        
        try:
            idn = self.inst.query("*IDN?")
            self.beep_success()
            print(f"Connection successful. Instrument ID: {idn.strip()}")
            return True
        except Exception as e:
            print(f"Connection failed: {e}")
            return False

def run_tests(inst, serial_number):
    print(f"Testing cell {serial_number}...")
    
    # 1. Open Circuit Voltage
    print("  Measuring OCV...")
    inst.source_current(0.0, kChargeComplianceLimit_volts)
    time.sleep(kVoltageSenseDwell_seconds)
    ocv = inst.measure_voltage()
    print(f"  OCV: {ocv:.4f} V")

    # 2. R0 Estimate
    print("  Measuring R0...")
    # Measure idle voltage for charge
    v_idle_charge = inst.measure_voltage()
    
    # Charge Pulse
    print(f"  Pulsing {kR0PulseCurrent_amps}A for {kR0PulseDuration_seconds}s...")
    v_load_charge = inst.source_pulse_current(kR0PulseCurrent_amps, kChargeComplianceLimit_volts, kR0PulseDuration_seconds)
    
    # Measure idle voltage for discharge
    print("  Measuring OCV...")
    v_idle_discharge = inst.measure_voltage()

    # Discharge Pulse
    print(f"  Pulsing {-kR0PulseCurrent_amps}A for {kR0PulseDuration_seconds}s...")
    v_load_discharge = inst.source_pulse_current(-kR0PulseCurrent_amps, kDischargeCompianceLimit_volts, kR0PulseDuration_seconds)

    r_charge = (v_load_charge - v_idle_charge) / kR0PulseCurrent_amps
    r_discharge = (v_idle_discharge - v_load_discharge) / kR0PulseCurrent_amps # Delta V / Delta I. Delta I is positive magnitude here.
    r0 = (r_charge + r_discharge) / 2.0
    print(f"  R0: {r0:.4f} Ohm")

    # 3. DCIR Test
    print("  Measuring DCIR...")
    # Measure idle voltage for charge
    v_idle_charge_dcir = inst.measure_voltage()
    
    # Charge
    print(f"  Sourcing {kDcirCurrent_amps}A for {kDcirDuration_seconds} seconds...")
    inst.source_current(kDcirCurrent_amps, kChargeComplianceLimit_volts)
    inst.output_on()
    time.sleep(kDcirDuration_seconds)
    v_load_charge_dcir = inst.measure_voltage()
    inst.output_off()

    # Measure idle voltage for discharge
    v_idle_discharge_dcir = inst.measure_voltage()

    # Discharge
    print(f"  Sourcing {-kDcirCurrent_amps}A for {kDcirDuration_seconds} seconds...")
    inst.source_current(-kDcirCurrent_amps, kDischargeCompianceLimit_volts)
    inst.output_on()
    time.sleep(kDcirDuration_seconds)
    v_load_discharge_dcir = inst.measure_voltage()
    inst.output_off()

    r_charge_dcir = (v_load_charge_dcir - v_idle_charge_dcir) / kDcirCurrent_amps
    r_discharge_dcir = (v_idle_discharge_dcir - v_load_discharge_dcir) / kDcirCurrent_amps
    dcir = (r_charge_dcir + r_discharge_dcir) / 2.0
    print(f"  DCIR: {dcir:.4f} Ohm")

    results = {
        "Serial Number": serial_number,
        "OCV (V)": ocv,
        "R0 (Ohm)": r0,
        "R0 Charge (Ohm)": r_charge,
        "R0 Discharge (Ohm)": r_discharge,
        "DCIR (Ohm)": dcir,
        "DCIR Charge (Ohm)": r_charge_dcir,
        "DCIR Discharge (Ohm)": r_discharge_dcir
    }
    
    return results

def main():
    parser = argparse.ArgumentParser(description="Battery Cell Testing Script")
    parser.add_argument("output_csv", help="Path to the output CSV file")
    parser.add_argument("--resource", default="GPIB0::24::INSTR", help="VISA resource string for Keithley 2430")
    parser.add_argument("--mock", action="store_true", help="Run in mock mode without hardware")
    parser.add_argument("--terminals", choices=['front', 'rear'], default='front', help="Select front or rear terminals (default: front)")
    parser.add_argument("--test-connection", action="store_true", help="Test connection to the instrument and exit")
    args = parser.parse_args()

    # Initialize CSV
    # Initialize CSV
    fieldnames = ["Serial Number", "OCV (V)", "R0 (Ohm)", "R0 Charge (Ohm)", "R0 Discharge (Ohm)", "DCIR (Ohm)", "DCIR Charge (Ohm)", "DCIR Discharge (Ohm)"]
    
    # Check if file exists to decide whether to write header
    try:
        with open(args.output_csv, 'x', newline='') as csvfile:
            writer = csv.DictWriter(csvfile, fieldnames=fieldnames)
            writer.writeheader()
    except FileExistsError:
        pass # Append to existing file

    try:
        inst = Keithley2430(args.resource, mock=args.mock, terminals=args.terminals)
        
        if args.test_connection:
            success = inst.test_connection()
            sys.exit(0 if success else 1)

        while True:
            try:
                serial_number = input("Scan barcode (or 'q' to quit): ").strip()
                if serial_number.lower() == 'q':
                    break
                if not serial_number:
                    continue

                results = run_tests(inst, serial_number)
                
                with open(args.output_csv, 'a', newline='') as csvfile:
                    writer = csv.DictWriter(csvfile, fieldnames=fieldnames)
                    writer.writerow(results)
                
                print(f"Test complete for {serial_number}. Results saved.")
                inst.beep_success()
                
            except KeyboardInterrupt:
                break
            except Exception as e:
                print(f"Error testing cell: {e}")

    except Exception as e:
        print(f"Failed to initialize instrument: {e}")
    finally:
        if 'inst' in locals():
            inst.close()

if __name__ == "__main__":
    main()

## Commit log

2025-08-16 Update README and add first pass at BOM
    [bill-of-materials.xlsx]
2025-08-16 Update sourcing for bus bars
    [bill-of-materials.xlsx, upper basic collector.step, upper end collector(Mirror).step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]
2025-08-23 Made some CAD progress; updated the README
2025-09-09 Create and populate information on serialization
    [serial_labels.csv]
2026-01-04 First full CAD commit, plus some software
    [cell_data.csv, modules.csv]
2026-02-14 Start including some of the electronics package
    [4ch_flyback.SchDoc, bms_afe_tester-1_0.PrjPcb, bms_companion-1_0.PcbDoc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]
2026-02-14 BMS schematic
    [adc_mcp3913.SchDoc, analog_sensor_input.SchDoc, bms_mainboard-1_0.PrjPcb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]
2026-02-15 Schematic tweaks resulting from layout
    [bms_mainboard-1_0.PrjPcb, can_tcan1462v.SchDoc, conn_harness_lv.SchDoc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]
2026-02-24 Refinements resulting from layout
    [bms_mainboard-1_0.PrjPcb, conn_harness_lv.SchDoc, hv_architecture.SchDoc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]
2026-03-01 Starting work on jlcpcb libraries
    [bms_mainboard-1_0.PrjPcb, capacitor.PcbLib, capacitor.SchLib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]
2026-03-02 Update bms_afe_tester to new dblib
    [bms_afe_tester-1_0.PrjPcb, capacitor.SchLib, capacitors.csv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]
2026-03-02 Migrate bms_afe to new dblib
    [bms_companion-1_0.PrjPcb, comm_connector.SchDoc, top.SchDoc]
2026-03-02 Rename files within bms_afe project
    [bms_afe-1_0.PrjPcb]
2026-03-06 Add FB; adjust pinouts
    [bms_mainboard-1_0.PrjPcb, isolator_si8662.SchDoc]
2026-03-14 Mostly migrate to new dblib components
    [adc_mcp3913.SchDoc, analog_sensor_input.SchDoc, bms_mainboard-1_0.PrjPcb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]
2026-03-15 Futzing with harness pinouts to optimize layout
    [conn_harness_lv.SchDoc, eth_100base-tx_magnetics.SchDoc, eth_ksz8567r_switch.SchDoc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]
2026-03-15 Updates for bms_afe-1_0 ordering
    [bom-bms_afe-1_0.xlsx, pnp-bms_afe-1_0.csv]
2026-03-15 Updated bms_afe_tester-1_0 while placing an order
    [bms_afe_tester-1_0.PrjPcb, bom-bms_afe_tester-1_0.xlsx, conn_usbc.SchDoc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]
2026-03-27 Remove vestigial connection to array on top sheet
    [hv_architecture.SchDoc, top.SchDoc]
2026-04-03 Worked on plane
    [hv_architecture.SchDoc, hv_bleed.SchDoc, pmic_tps65263_buck.SchDoc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]
2026-04-03 Routing complete
    [gnss_quectel_lc29hea.SchDoc]
2026-04-04 Purchasing cleanup
    [adc_mcp3913.SchDoc, bms_afe_tester-1_0.PrjPcb, bms_mainboard-1_0.PrjPcb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]
2026-04-05 Substantial update
    [adc_mcp3913.SchDoc, bill-of-materials.xlsx, bms_afe_tester-1_0.PrjPcb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]
2026-04-05 More fab updates
    [bom-bms-1_0_self-stuff.xlsx, pmic_vicor_brick.SchDoc]
2026-04-19 Various updates
    - Fixed bug in AFE where RX needed to be connected to CVDD.
    - Added SWD header security tape frame to BMS mainboard.
    - Updated BOM for hardware for security tape frame and reduced NTC count.
    - Created new IOC file for BGA STM32 on mainboard
    - Fixed off-by-one error on port A on mainboard STM32F4.
    [bill-of-materials.xlsx, bom-bms-1_0_self-stuff.xlsx, mcu_stm32f4.SchDoc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]
2026-05-10 BMS order commit
    [bom-bms-1_0_jlcpcb.xlsx, pnp-bms_1-0.csv]
2026-05-17 Started work on bms_afe_tester-1_1
    [bms_afe_tester-1_1.PrjPcb, cell_simulator.SchDoc, conn_usbc.SchDoc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]
2026-05-17 Update variants and fonts
    [bms_afe_tester-1_1.PrjPcb, cell_simulator.SchDoc, conn_usbc.SchDoc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]
2026-06-03 Starting revisions
    [adc_mcp3913.SchDoc, analog_sensor_input.SchDoc, bms_afe_tester-1_1.PrjPcb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]
2026-06-05 Post-bringup fixes
    [bridge_bq79600.SchDoc, current_mp6519.SchDoc, gnss_quectel_lc29hea.SchDoc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]
2026-06-10 Continued bringup edits
    [adc_mcp3913.SchDoc, analog_lvb_sense.SchDoc, bms_mainboard-1_1.PrjPcb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]
2026-06-10 Switched to red PPS LED.
    [gnss_quectel_lc29hea.SchDoc]
2026-06-10 Added PPS test point
    [top.SchDoc]
2026-06-11 More post-bringup tweaks
    [conn_harness_lv.SchDoc, eth_ksz8567r_switch.SchDoc, mcu_stm32f4.SchDoc]
2026-06-12 Added bidirectional level shifter to SWD and UART buses
    [st-link-v2.SchDoc, top.SchDoc]
2026-06-15 Continued improvements
    [bill-of-materials.xlsx, st-link-v2.SchDoc]
2026-06-18 Changed bleed resistor value
    [hv_bleed.SchDoc]
